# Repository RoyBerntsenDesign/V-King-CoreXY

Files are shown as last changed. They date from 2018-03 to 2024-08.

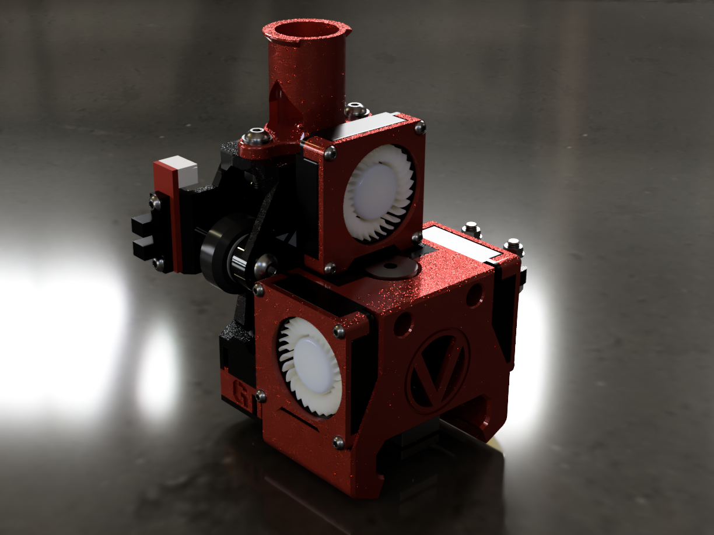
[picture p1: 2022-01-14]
Image Library/Renders/X-Carrier_Assy 4010 Fan Version 00.png

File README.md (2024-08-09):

# V-King Pro 3d Printer
The non rod CoreXY V-Slot 3d Printer by Roy Berntsen
In this repository you will find the print files and documentation for the V-King 3D printer

Here is a link to the Fusion 360 3d Model for viewing and also download: https://a360.co/3YxhjgS

You can be a supporter of the develompent on patreon here: https://www.patreon.com/pro3d?fan_landing=true
Or if you would buy me a coffe to keep the pace going in this project:

<a href="https://www.buymeacoffee.com/pro3d" target="_blank">Buy Me A Coffee</a>

Community links: https://www.facebook.com/vking3d/ - https://www.facebook.com/groups/viking3d/
Here is a video covering the basics and benefits of this design: https://youtu.be/wINF7qM0DQU

All files are released according to the following license unless specified differently in the file or directory:
CC-by-NC: http://creativecommons.org/licenses/by-nc/3.0/

Roy Berntsen - Research and Development

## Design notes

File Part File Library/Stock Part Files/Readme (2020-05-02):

Slicer Recomendations
Material: CPE, PETG or similar as is more durable than PLA

Walls:      2 mm Shell
Bottom/Top: 2 mm shell
Infill:		25% - 100%

You do need a good calibrated extruder as parts are tight so check your flow
All parts are modeled with tolerance to fit - Some holes are designed to be drilled

Suffix Explanation:
Example
- Filename_1x_SN_BN_100% = 1x of this part, Support NO, Brim NO, Infill 100%
- Filename_2x_SA_BY_25% = 2x of this part, Support ALL, Brim YES, Infill 25%
- Filename_3x_SB_BO_50% = 3x of this part, Support BUILDPLATE, Brim OPTIONAL, Infill 50%

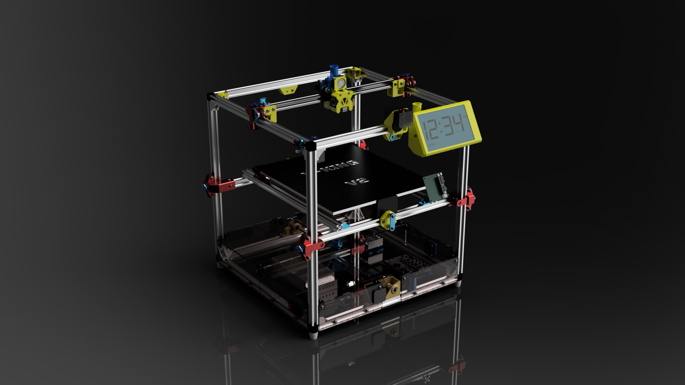
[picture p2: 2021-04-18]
V-King V2.0 00.PNG

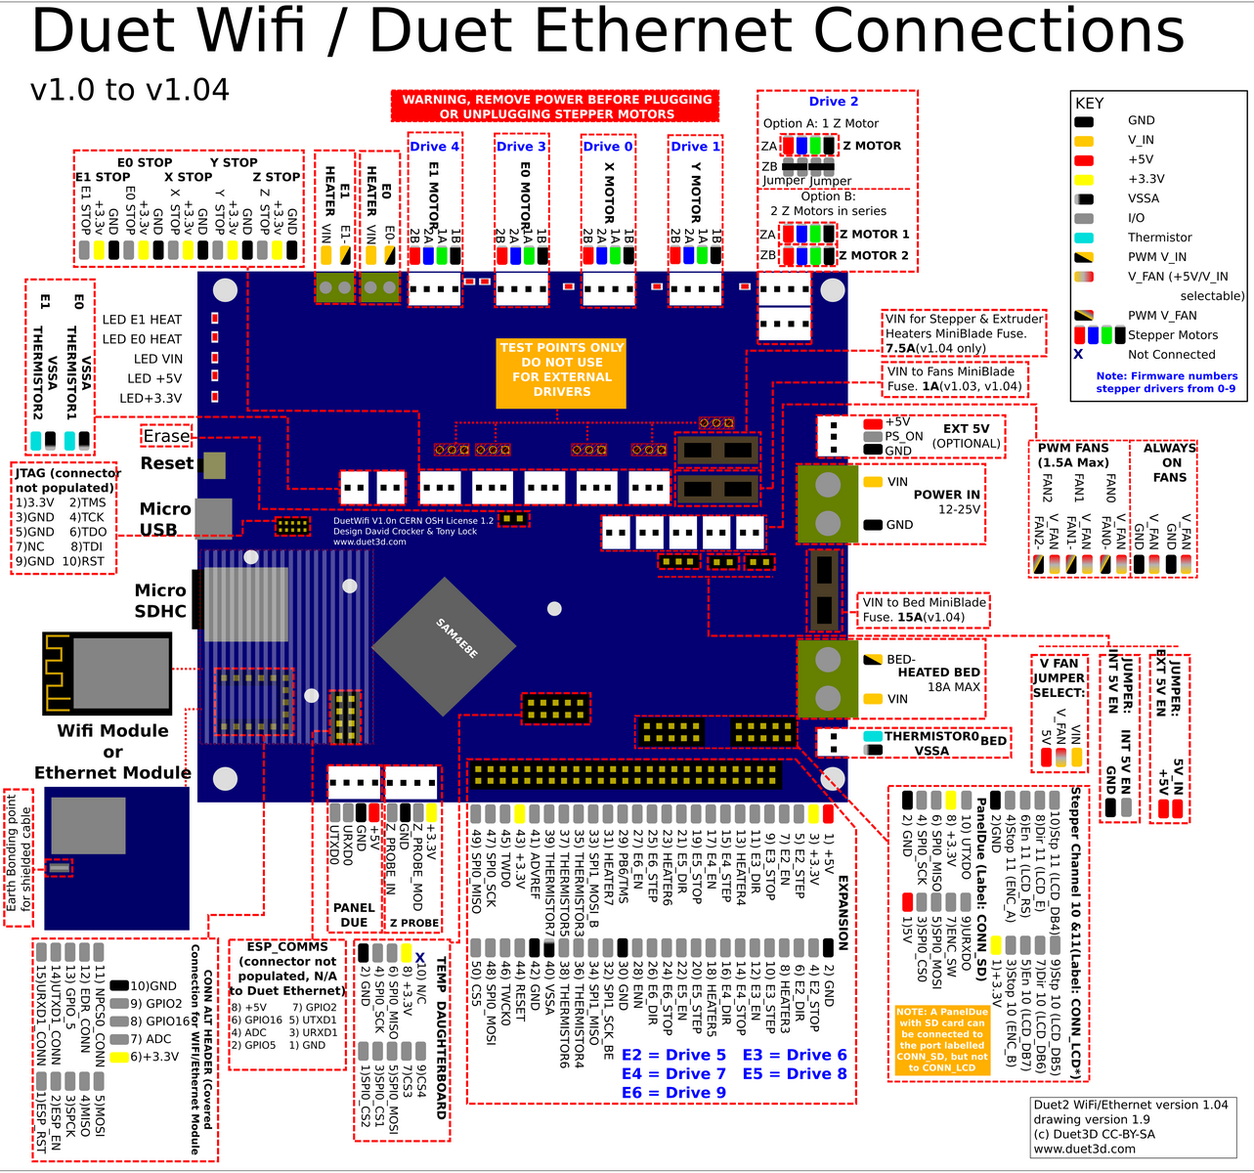
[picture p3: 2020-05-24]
Firmware Files/RRF-Duet/DuetWF Connection.png

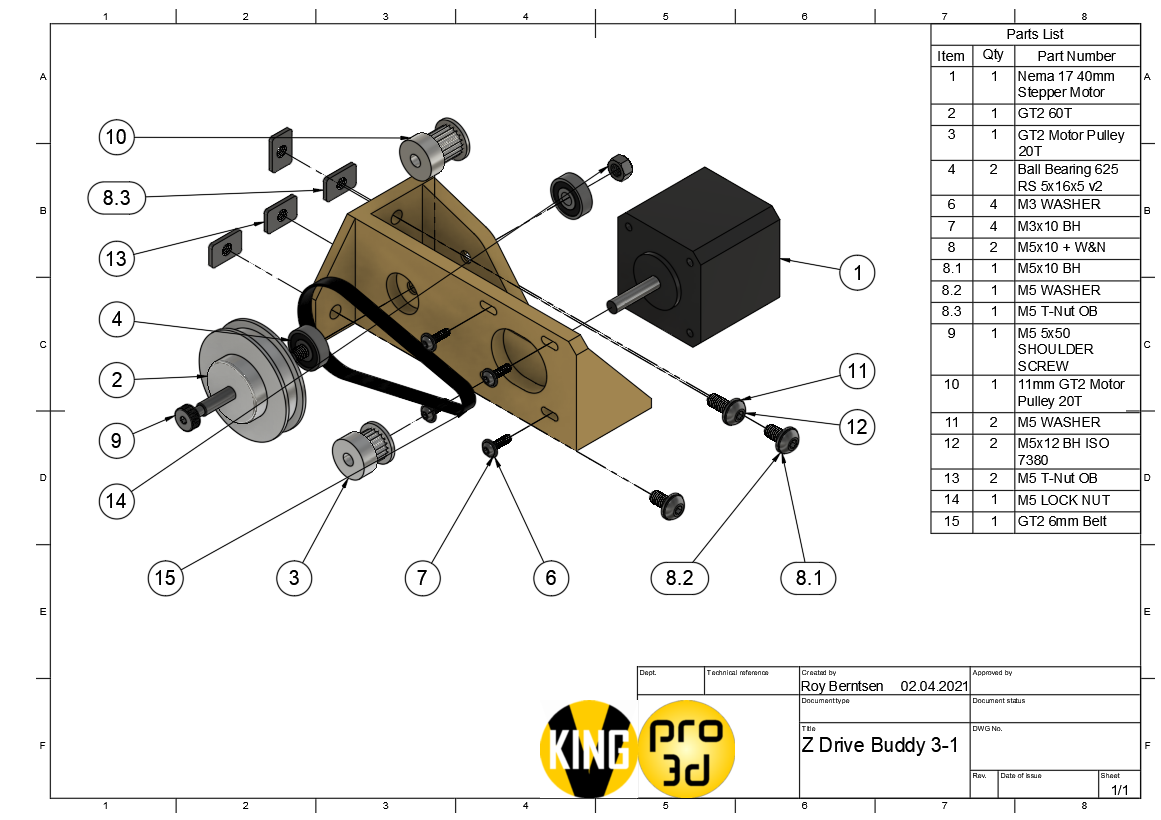
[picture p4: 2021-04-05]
Document Library/Drawings/GT2 Z BeltGear 00.png

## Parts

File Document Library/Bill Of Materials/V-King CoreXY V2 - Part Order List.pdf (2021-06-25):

V-King (https://www.buymeacoffee.com/pro3d) CoreXY Part List

MakerSupplies Mechanical Kit (https://makersupplies.dk/corexy-3d-printer/351-corexy-3d-printer-base-mechanical-kit-for-v-king-corexy-3d-printer.html) | <<-- ALL HARDWARE KIT HERE | | | $395,00
Component Part Name | Description | Quantity | Shop Link | Price | Optional Component | Price2
Belt GT2 Idler Smooth | GT2 20T Smooth Idler | 6 | 6Pcs 7mm Without T (http://s.click.aliexpress.com/e/b6kkkvj2) | $22,00
Belt GT2 Idler Thoothed | GT2 20T Thoothed Idler | 8 | 8Pcs 7mm With T (http://s.click.aliexpress.com/e/b6kkkvj2) | $25,00
Belt GT2 Stepper Motor Pulley | GT2 20T 6W 5mm Bore | 4 | 4 x 5 BORE (http://s.click.aliexpress.com/e/zhwLX5q) | $13,00
Belt GT2 Timing Belt 6mm | 10M 2GT Timing Belt 6W | 10 | 10M-6MM-2GT (http://s.click.aliexpress.com/e/cXFkq2jO) | $30,00
Belt Idler Precision Shim | 6,5mm OD/ 5mm ID Shim | 80 | (4x20) 6,5x5x1 Option Shim (https://www.aliexpress.com/item/32874078293.html?spm=2114.12010612.8148356.4.6b2842c5OC71Xu) | $20,00 | 200 pcs is same price (https://www.aliexpress.com/item/32874190317.html?spm=2114.12010612.8148356.2.6b2842c5nKhsGR)
Bowden Tube | 1.9ID 4OD Filament Tube | 1 | ID 1.9 OD 4 (http://s.click.aliexpress.com/e/cSMR0cdw) | $2,50
Cable Loom Tube | Sleeve for cables to hotend | 1 | 20mmx1m Cable Loom (https://s.click.aliexpress.com/e/_dTFkJul) | $2,50
Cable Nylon Sleeve | Sleeve for Heatbed cables | 1 | 5meter, 10mm Sleeve (https://s.click.aliexpress.com/e/_dVKCa4n) | $3,00
Controller Board | Duet WIFI Clone w/TMC2660 | 1 | MKS DUET WIFI Clone (https://s.click.aliexpress.com/e/_AsHC5n) | $60,00
Endstop Optical | XY(Z) Endstops | 3 | 6Pack Endstops (http://s.click.aliexpress.com/e/Im2VNR3) | $4,00
Extruder | BMG Clone Filament Extruder | 1 | TriangleLab BMG (https://s.click.aliexpress.com/e/_97d9QB) | $31,00
Fan for Controller Cooling | 4010 Axial Fan 12/24V | 1 | 24V Controller Fan (http://s.click.aliexpress.com/e/i1Q2ghS) | $3,00
Fan for Hotend Cooling | 4010 Blower Fan 12/24V | 1 | 24V 40x10 Blower (http://s.click.aliexpress.com/e/kHMx4q7O) | $2,00
Fan for Layer Cooling | 3010 Blower Fan 5/12 24V | 2 | 24V 30x30x10 (http://s.click.aliexpress.com/e/bele3ZZI) | $10,00
Heatbed Build Plate | Milled Cast Aluminum | 1 | 360x410x8 mm (https://makersupplies.dk/metal/816-metal-cnc-milled-cast-aluminum-plate.html) | $98,00
Heatbed Silicon Heater | 350*400 110V/220V Heater | 1 | 220V/110V (http://s.click.aliexpress.com/e/bWGHdGPI) | $16,00
Hotend | Dragon Hotend Clone | 1 | 1,75 24V Trianglelab Dragon (https://s.click.aliexpress.com/e/_ASb1l5) | $73,00
NEMA 17 1.8 A Stepper Motor | Stepper motor 1.5 Amp | 1x5 | 5Pack & Cable (https://s.click.aliexpress.com/e/_dXEZHHb) | $30,00
Power Switch | 10A 250VAC Fused Switch | 1 | 10A Fused Switch (http://s.click.aliexpress.com/e/blNcy7Lw) | $8,50
Powersupply | 24V 240W PSU | 1 | 24V 10A 240W (http://s.click.aliexpress.com/e/4GAsFeg) | $20,00
Safety Fuse | Thermal Safety Fuse for SSR | 1 | 135 Deg Fuse (http://s.click.aliexpress.com/e/bu7dz62U) | $2,00
Solid State Relay | Silicone Heater Relay Switch | 1 | SSR 40DA (http://s.click.aliexpress.com/e/ckUQTj4c) | $3,50
Worm Gear | 1:20 Worm Gear Set | 1 | Worm Gear (https://s.click.aliexpress.com/e/_A5bZW3) | $13,00 | High End Gear (https://makersupplies.dk/gear/361-gear-worm-gear-120-japan.html) | $51,00
Worm Gear Bearings | 5id-16od-5w Ball bearings | 10 | Worm Gear Bearings (http://s.click.aliexpress.com/e/c5afxP5q) | $4,00
Worm Gear Rod | 5mm X 555 mm Steel rod | 1 | Worm Gear Rod (https://rover.ebay.com/rover/1/711-53200-19255-0/1?icep_id=114&ipn=icep&toolid=20004&campid=5338443015) | $20,00
Z Leveling Probe | 3D Touch Leveling Probe | 1 | 3D Touch (http://s.click.aliexpress.com/e/bhxMAOUo) | $12,00
Component Total Price | | | | $528,00
Price inclusive mech kit | | | | USD 923,00

If you like to support - Buy me a coffe here:

https://www.buymeacoffee.com/pro3d

Research, Development & Design by:
Roy Berntsen M.Sc. Engineering Designer (https://www.buymeacoffee.com/pro3d)

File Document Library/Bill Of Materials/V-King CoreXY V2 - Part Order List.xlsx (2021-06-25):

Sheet: BOM Overview
V-King V2 Build Price Estimate
340x390x330 Build Volume
All aluminum, wheels and fastners | USD 395
Components Example Price: | USD 528
Cables and Connectors Estimated Price | USD 50
Tools - Add your number | USD 0
Sub Total Example Price | USD 973
Research - Development & Design by:
Roy Berntsen

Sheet: Complete Part List
 |  |  | V-King CoreXY Part List
MakerSupplies Mechanical Kit (https://makersupplies.dk/corexy-3d-printer/351-corexy-3d-printer-base-mechanical-kit-for-v-king-corexy-3d-printer.html) | <<-- ALL HARDWARE KIT HERE |  |  | $395.00
Component Part Name | Description | Quantity | Shop Link | Price | Optional Component | Price2
Belt GT2 Idler Smooth | GT2 20T Smooth Idler | 6 | 6Pcs 7mm Without T (http://s.click.aliexpress.com/e/b6kkkvj2) | $22.00
Belt GT2 Idler Thoothed | GT2 20T Thoothed Idler | 8 | 8Pcs 7mm With T (http://s.click.aliexpress.com/e/b6kkkvj2) | $25.00
Belt GT2 Stepper Motor Pulley | GT2 20T 6W 5mm Bore | 4 | 4 x 5 BORE (http://s.click.aliexpress.com/e/zhwLX5q) | $13.00
Belt GT2 Timing Belt 6mm | 10M 2GT Timing Belt 6W | 10 | 10M-6MM-2GT (http://s.click.aliexpress.com/e/cXFkq2jO) | $30.00
Belt Idler Precision Shim | 6,5mm OD/ 5mm ID Shim | 80 | (4x20) 6,5x5x1 Option Shim (https://www.aliexpress.com/item/32874078293.html?spm=2114.12010612.8148356.4.6b2842c5OC71Xu) | $20.00 | 200 pcs is same price (https://www.aliexpress.com/item/32874190317.html?spm=2114.12010612.8148356.2.6b2842c5nKhsGR)
Bowden Tube | 1.9ID 4OD Filament Tube | 1 | ID 1.9 OD 4 (http://s.click.aliexpress.com/e/cSMR0cdw) | $2.50
Cable Loom Tube | Sleeve for cables to hotend | 1 | 20mmx1m Cable Loom (https://s.click.aliexpress.com/e/_dTFkJul) | $2.50
Cable Nylon Sleeve | Sleeve for Heatbed cables | 1 | 5meter, 10mm Sleeve (https://s.click.aliexpress.com/e/_dVKCa4n) | $3.00
Controller Board | Duet WIFI Clone w/TMC2660 | 1 | MKS DUET WIFI Clone (https://s.click.aliexpress.com/e/_AsHC5n) | $60.00
Endstop Optical | XY(Z) Endstops | 3 | 6Pack Endstops (http://s.click.aliexpress.com/e/Im2VNR3) | $4.00
Extruder | BMG Clone Filament Extruder | 1 | TriangleLab BMG (https://s.click.aliexpress.com/e/_97d9QB) | $31.00
Fan for Controller Cooling | 4010 Axial Fan 12/24V | 1 | 24V Controller Fan (http://s.click.aliexpress.com/e/i1Q2ghS) | $3.00
Fan for Hotend Cooling | 4010 Blower Fan 12/24V | 1 | 24V 40x10 Blower (http://s.click.aliexpress.com/e/kHMx4q7O) | $2.00
Fan for Layer Cooling | 3010 Blower Fan 5/12 24V | 2 | 24V 30x30x10 (http://s.click.aliexpress.com/e/bele3ZZI) | $10.00
Heatbed Build Plate | Milled Cast Aluminum | 1 | 360x410x8 mm (https://makersupplies.dk/metal/816-metal-cnc-milled-cast-aluminum-plate.html) | $98.00
Heatbed Silicon Heater | 350*400 110V/220V Heater | 1 | 220V/110V (http://s.click.aliexpress.com/e/bWGHdGPI) | $16.00
Hotend | Dragon Hotend Clone | 1 | 1,75 24V Trianglelab Dragon (https://s.click.aliexpress.com/e/_ASb1l5) | $73.00
NEMA 17 1.8 A Stepper Motor | Stepper motor 1.5 Amp | 1x5 | 5Pack & Cable (https://s.click.aliexpress.com/e/_dXEZHHb) | $30.00
Power Switch | 10A 250VAC Fused Switch | 1 | 10A Fused Switch (http://s.click.aliexpress.com/e/blNcy7Lw) | $8.50
Powersupply | 24V 240W PSU | 1 | 24V 10A 240W (http://s.click.aliexpress.com/e/4GAsFeg) | $20.00
Safety Fuse | Thermal Safety Fuse for SSR | 1 | 135 Deg Fuse (http://s.click.aliexpress.com/e/bu7dz62U) | $2.00
Solid State Relay | Silicone Heater Relay Switch | 1 | SSR 40DA (http://s.click.aliexpress.com/e/ckUQTj4c) | $3.50
Worm Gear | 1:20 Worm Gear Set | 1 | Worm Gear (https://s.click.aliexpress.com/e/_A5bZW3) | $13.00 | High End Gear (https://makersupplies.dk/gear/361-gear-worm-gear-120-japan.html) | $51.00
Worm Gear Bearings | 5id-16od-5w Ball bearings | 10 | Worm Gear Bearings (http://s.click.aliexpress.com/e/c5afxP5q) | $4.00
Worm Gear Rod | 5mm X 555 mm Steel rod | 1 | Worm Gear Rod (https://rover.ebay.com/rover/1/711-53200-19255-0/1?icep_id=114&ipn=icep&toolid=20004&campid=5338443015) | $20.00
Z Leveling Probe | 3D Touch Leveling Probe | 1 | 3D Touch (http://s.click.aliexpress.com/e/bhxMAOUo) | $12.00
Component Total Price |  |  |  | $528.00
Price inclusive mech kit |  |  |  | USD 923.00

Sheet: Fasteners BOM
Part name | Quantity | Order Quantity | Est. Price
M2,0x06 BH | 2 |  | 0.15 | 0.3
M2,5x12 BH | 2 |  | 0.15 | 0.3
M2,5x16 BH | 2 |  | 0.15 | 0.3
M3 Lock Nut | 2 |  | 0.15 | 0.3
M3 NUT | 14 |  | 0.15 | 2.1
M3 WASHER | 14 |  | 0.15 | 2.1
M3x08 BH | 10 |  | 0.15 | 1.5
M3x12 BH | 4 |  | 0.15 | 0.6
M3x20 BH | 6 |  | 0.15 | 0.9
M3x25 BH | 4 |  | 0.15 | 0.6
M4 NUT | 4 |  | 0.15 | 0.6
M4 WASHER | 4 |  | 0.15 | 0.6
M4x12 BH | 2 |  | 0.15 | 0.3
M4x16 BH | 4 |  | 0.15 | 0.6
M5 Hammer-Nut | 16 | 25 | 0.15 | 2.4
M5 Lock Nut | 23 | 25 | 0.15 | 3.45
M5 Nut | 19 | 25 | 0.15 | 2.85
M5 T-Nut OB | 110 |  | 0.15 | 16.5
M5 WASHER | 166 | 175 | 0.15 | 24.9
M5x08 Countersink | 24 |  | 0.15 | 3.6
M5x10 BH | 142 | 150 | 0.15 | 21.3
M5x20 Hex | 9 |  | 0.15 | 1.35
M5x25 BH | 13 |  | 0.15 | 1.95
M5x30 Button Head | 12 |  | 0.15 | 1.8
M5x35 BH | 2 |  | 0.15 | 0.3
M5x35 Hex | 4 |  | 0.15 | 0.6
M5x40 BH | 2 |  | 0.15 | 0.3
M5x6,5x1 Precision Shim | 73 | 80 | 0.15 | 10.95
Est sub total fastners: |  |  |  | $103.35

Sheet: Tools
Tools
Crimping Tool | PA-21 (http://rover.ebay.com/rover/1/711-53200-19255-0/1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) | 40

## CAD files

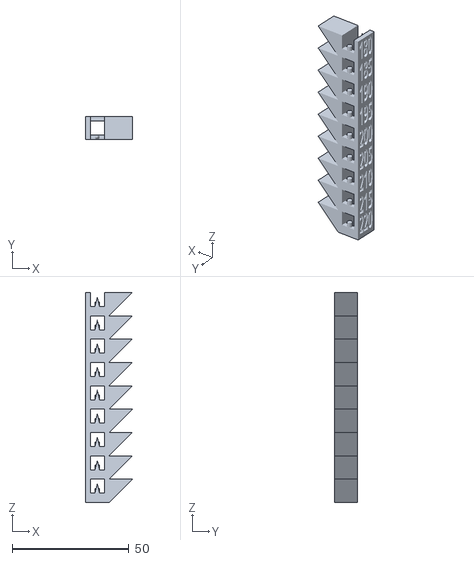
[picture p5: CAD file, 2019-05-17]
Calibration Files/Temp Tower.stl
20.0 x 10.0 x 90.0

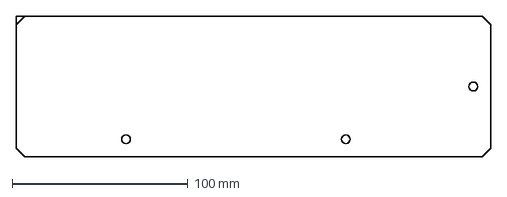
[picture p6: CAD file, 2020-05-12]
Document Library/Drawings/Cabinet Cut Pattern/Panel Side A_2x.dxf
270.0 x 80.0 mm

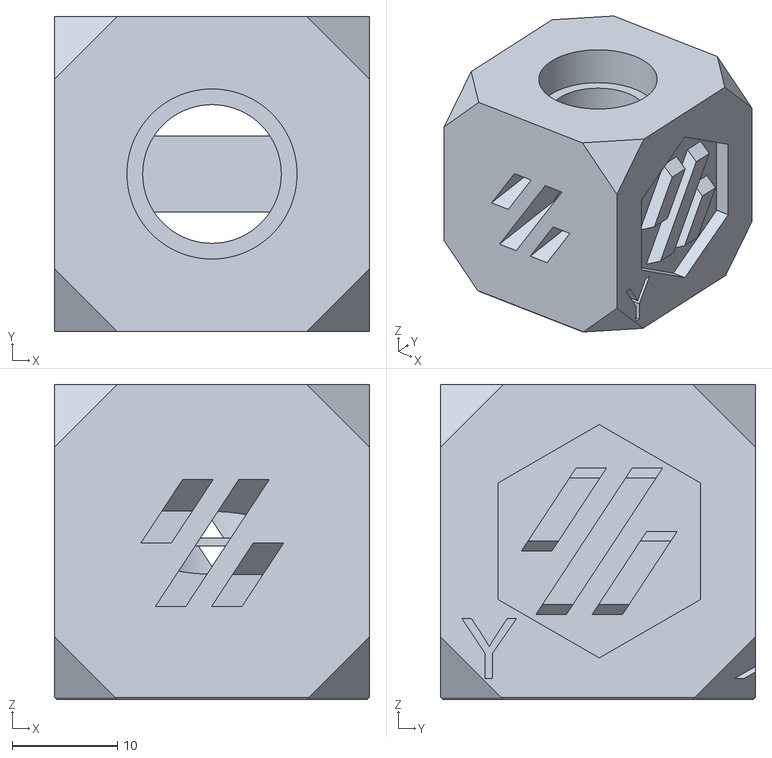
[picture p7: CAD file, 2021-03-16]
Part File Library/Calibration Files/Voron_Design_Cube_v7 (1).stl
30.0 x 30.0 x 30.0

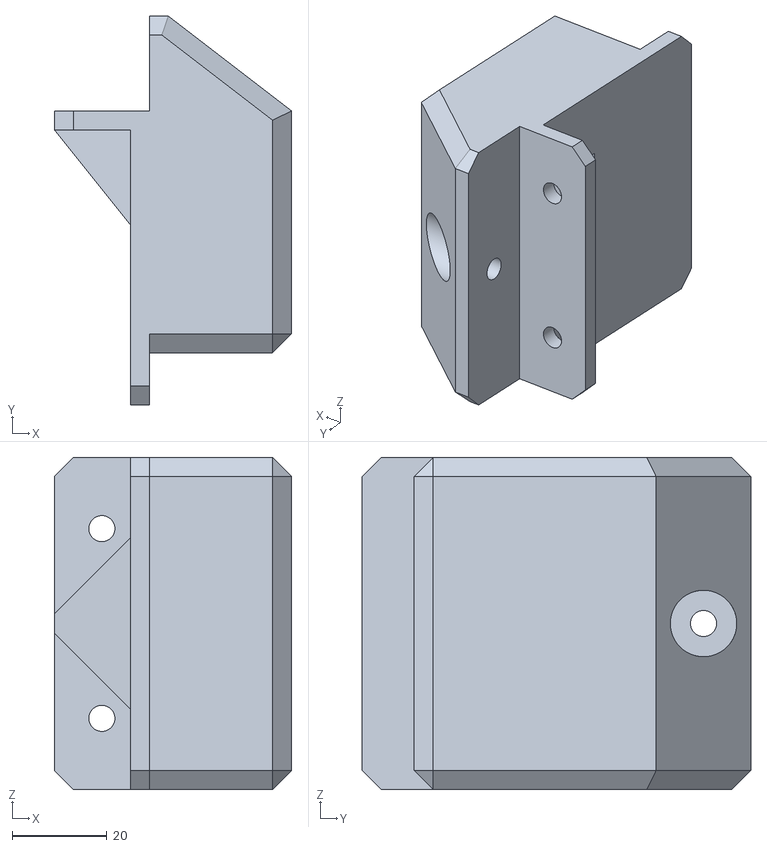
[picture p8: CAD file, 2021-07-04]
Part File Library/Discontinued Files/3P Center Bed Support V1.1_1x_SN_BN.stl
50.0 x 82.0 x 70.0

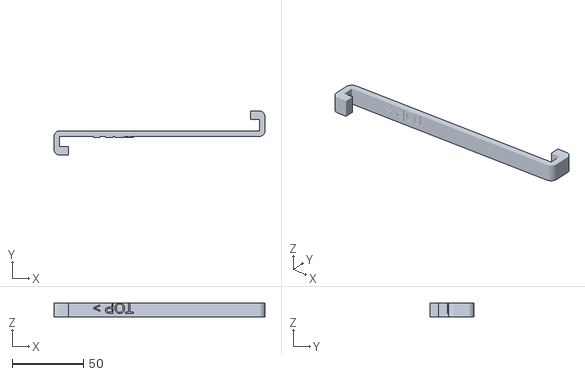
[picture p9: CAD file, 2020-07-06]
Part File Library/Optional Files/Bed Frame Hooks_4x_SN_BO.stl
148.0 x 31.0 x 10.0

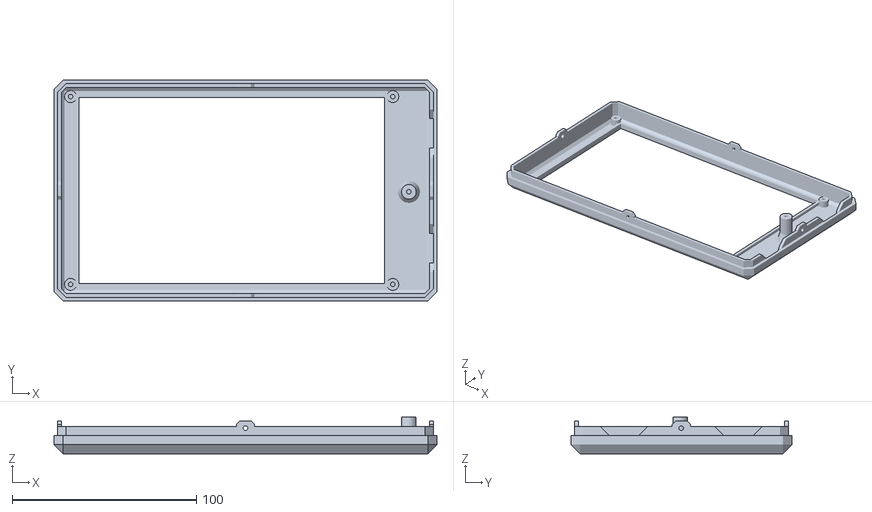
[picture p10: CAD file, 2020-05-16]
Part File Library/Optional Files/Panel Due 7in Cabinet Combo/Panel Due Cabinet Panel_1x_SN_BN.stl
208.0 x 120.0 x 20.0

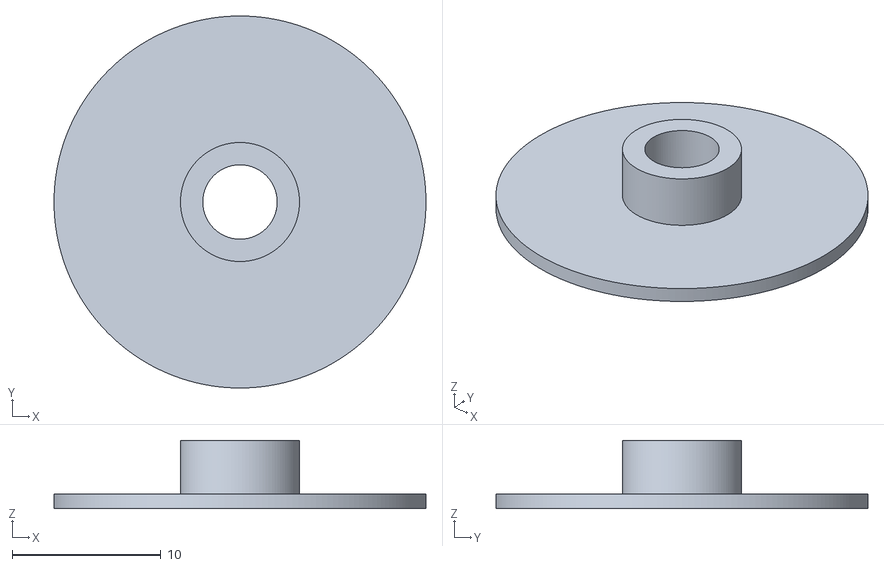
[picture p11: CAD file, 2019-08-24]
Part File Library/Optional Files/XY Belt Tensioner/608 Bearing Adapter_4x_SN_BN.stl
25.0 x 25.0 x 4.60

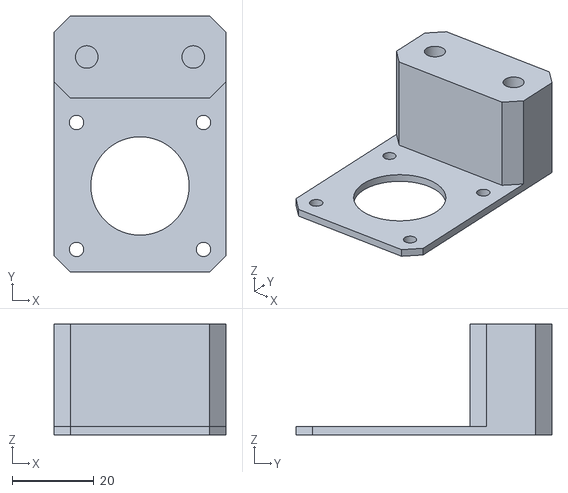
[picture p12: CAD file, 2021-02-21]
Part File Library/Stock Part Files/Base Frame Parts/Extruder Buddy_1x_SN_BN.stl
42.0 x 62.5 x 27.0

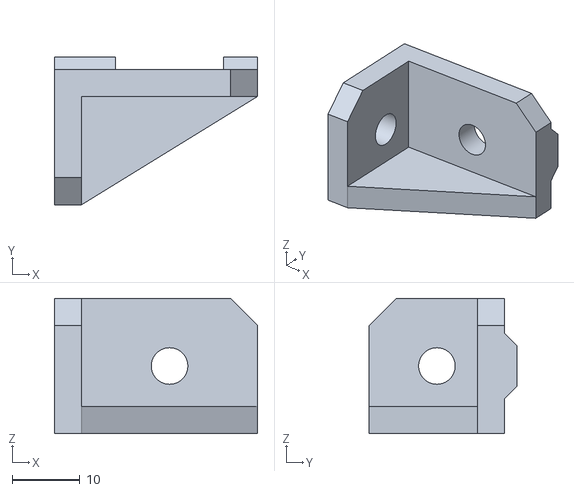
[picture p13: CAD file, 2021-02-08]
Part File Library/Stock Part Files/Bed Frame Parts/Bed L Bracket_4x_SN_BN.stl
30.0 x 21.8 x 20.0

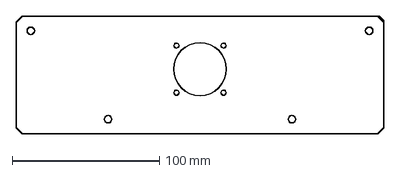
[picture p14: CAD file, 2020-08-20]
Part File Library/Stock Part Files/Bottom Cabinet Files/Cabinet Cut Pattern/Panel Side Fan_1x.dxf
250.0 x 80.0 mm

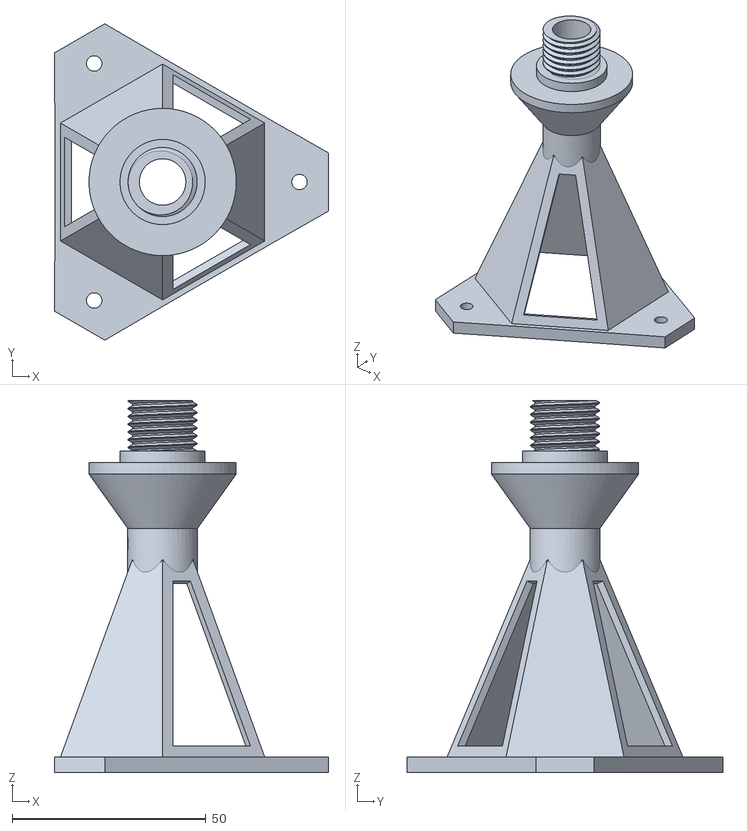
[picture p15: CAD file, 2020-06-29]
Part File Library/Stock Part Files/Bottom Cabinet Files/Cabinet Lid Support_1x_SN_BO.stl
70.7 x 81.7 x 96.0

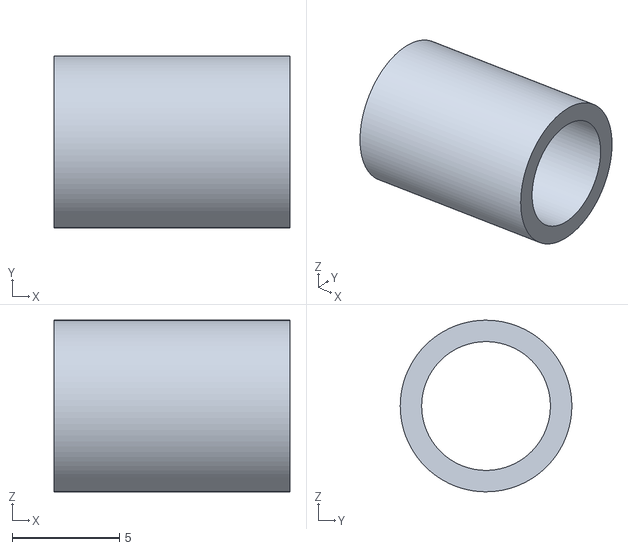
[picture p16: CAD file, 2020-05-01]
Part File Library/Stock Part Files/X Axis Parts/X Axis Idler Spacer_2x_SN_BY.stl
11.0 x 8.00 x 8.00

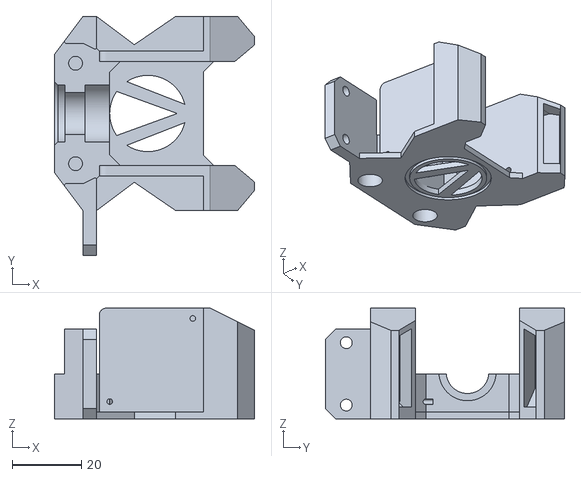
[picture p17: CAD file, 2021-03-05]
Part File Library/Stock Part Files/X Axis Parts/X Carrier/X Carrier Hotend Buddy_1x_SA_BN.stl
57.9 x 69.0 x 32.0

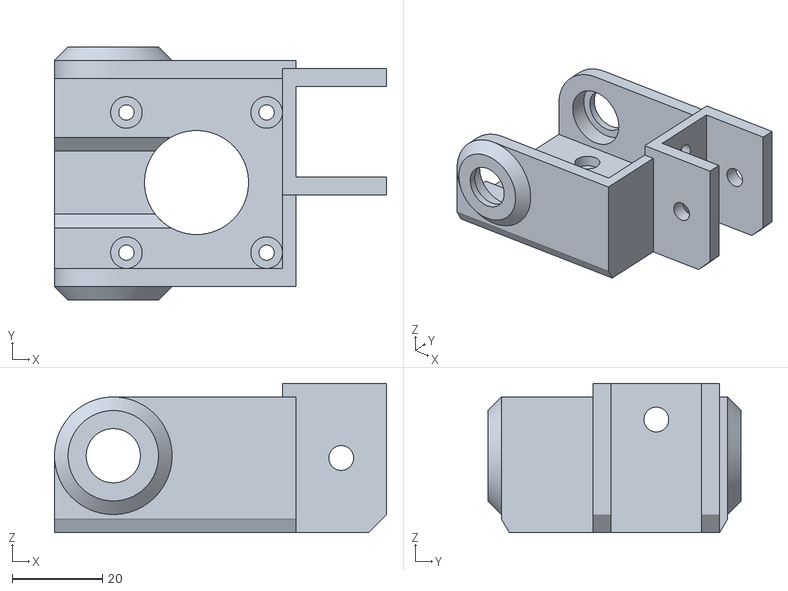
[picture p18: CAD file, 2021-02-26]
Part File Library/Stock Part Files/Z Drive Parts/Z Worm Gear Buddy_1x_SN_BN.stl
73.4 x 56.0 x 33.0

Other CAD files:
Part Print Files/Upgrade STL Files/Tablet Buddy.stl
Part Print Files/Z Part Files/Bed Belt Idler Support.stl
Source File Library/X Carrier Hotend Buddy.step
Source Files/Slider Fork v1.step
Calibration Files/3020 Cylinder.stl
Calibration Files/303010 Calibration Cube.stl
Calibration Files/Stringing_Test.stl
Calibration Files/xyzCalibration_cube.stl
Part File Library/Calibration Files/3020 Cylinder.stl
Part File Library/Calibration Files/303010 Calibration Cube.stl
Part File Library/Calibration Files/Retract four_square_cons.stl
Part File Library/Calibration Files/Stringing_Test.stl
Part File Library/Calibration Files/xyzCalibration_cube.stl
Part File Library/Calibration Files/z-wobble-test-square.stl
Part File Library/Calibration Files/z-wobble-test.stl
Part File Library/Optional Files/Panel Due 7in Cabinet Combo/Panel Due Cabinet Base_1x_SB_BN.stl
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

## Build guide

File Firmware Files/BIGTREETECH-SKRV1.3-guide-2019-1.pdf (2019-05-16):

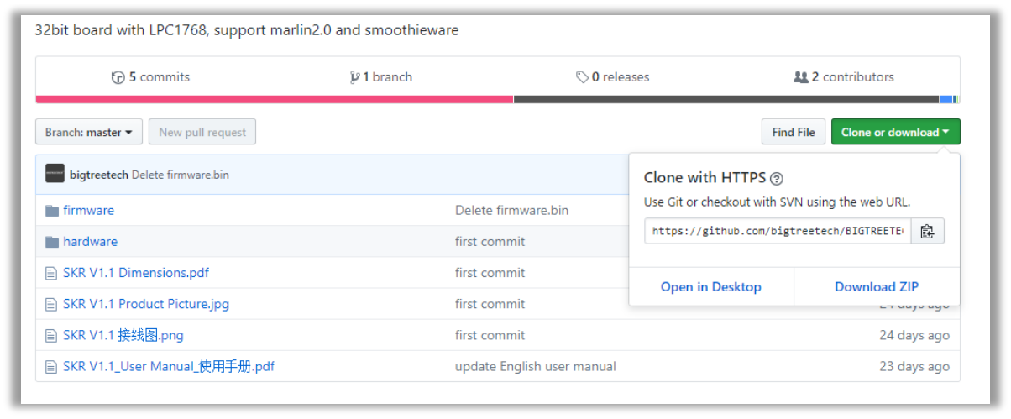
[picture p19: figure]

BIGTREETECH SKR V1.3 guide 2019 – V1 by Jupa Creations Page 1

BIGTREETECH/BIQU SKR V1.3 instruction guide by Jupa Creations

All official information like schematics and hardware about this 32 bits 3D printer mainboard can be found on the BIGTREETECH official GITHUB site. (https://github.com/bigtreetech/BIGTREETECH-SKR-V1.3)

This instruction guide is to show you how to install Marlin 2.0 firmware to the SKR V1.3 board in general. It does not take in account machine and other hardware specific settings!

You can use VSCode or Atom.IO + Platform IO to compile Marlin2.0 to BIGTREETECH/BIQU SKR V1.3

Intended for use with a REPRAP_DISCOUNT_FULL_GRAPHIC_SMART_CONTROLLER 128x64 LCD display by standard with two 10 wire ribbon cables.

Download the Marlin2.0 firmware from Marlin 2.0 github firmware version (https://github.com/MarlinFirmware/Marlin/tree/bugfix-2.0.x) and click.

Click “Download ZIP”

Remark if you use Octoprint, do not use the BIGTREETECH firmware version itself but download Marlin 2.0 github firmware version (https://github.com/MarlinFirmware/Marlin/tree/bugfix-2.0.x) and modify it to your needs.

When the download is complete, unzip the file to a known place.

N this example we use VScode

Download the VScode from https://code.visualstudio.com/Download. Choose the version which is compliant with your PC operating system.

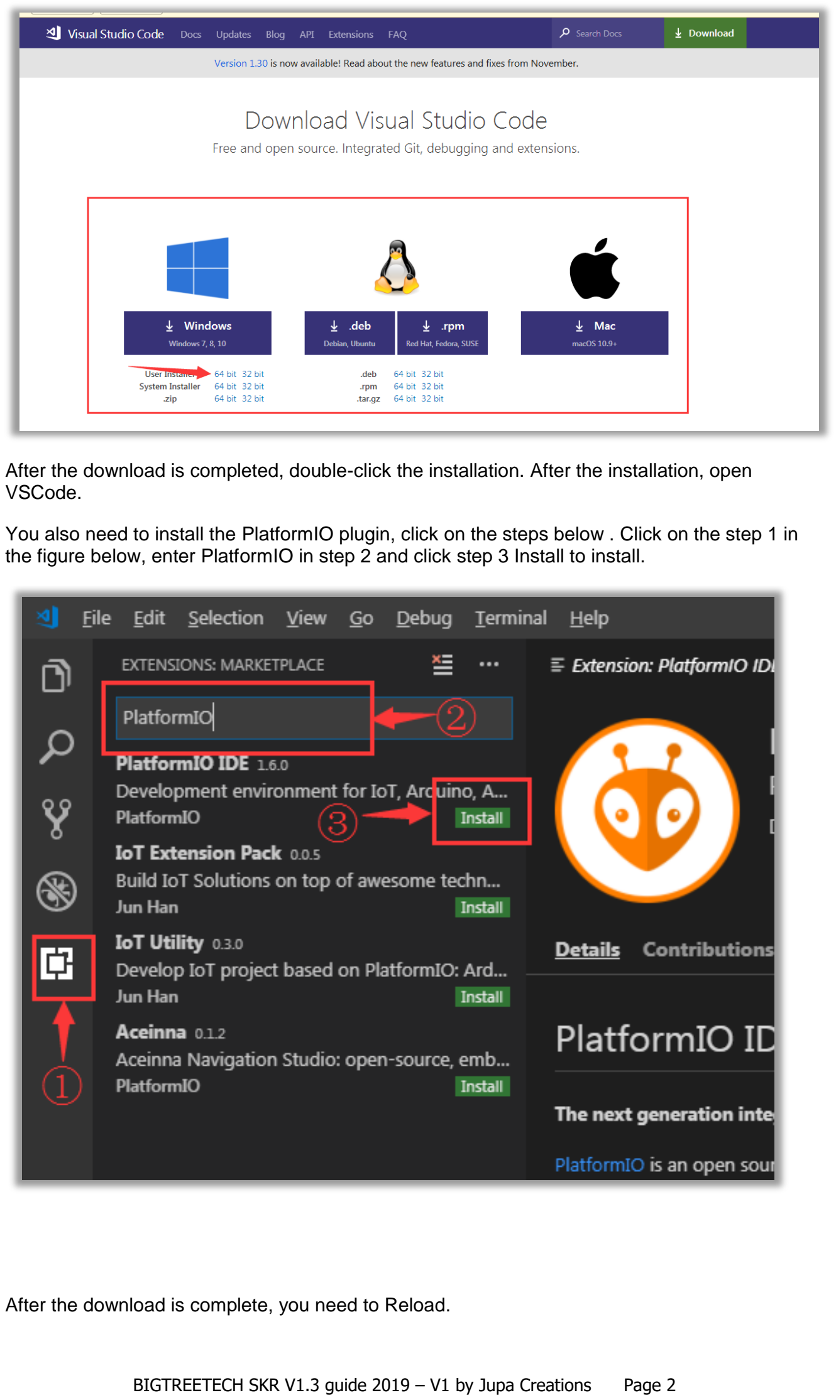
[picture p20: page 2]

BIGTREETECH SKR V1.3 guide 2019 – V1 by Jupa Creations Page 2

After the download is completed, double-click the installation. After the installation, open VSCode.

You also need to install the PlatformIO plugin, click on the steps below . Click on the step 1 in the figure below, enter PlatformIO in step 2 and click step 3 Install to install.

After the download is complete, you need to Reload.

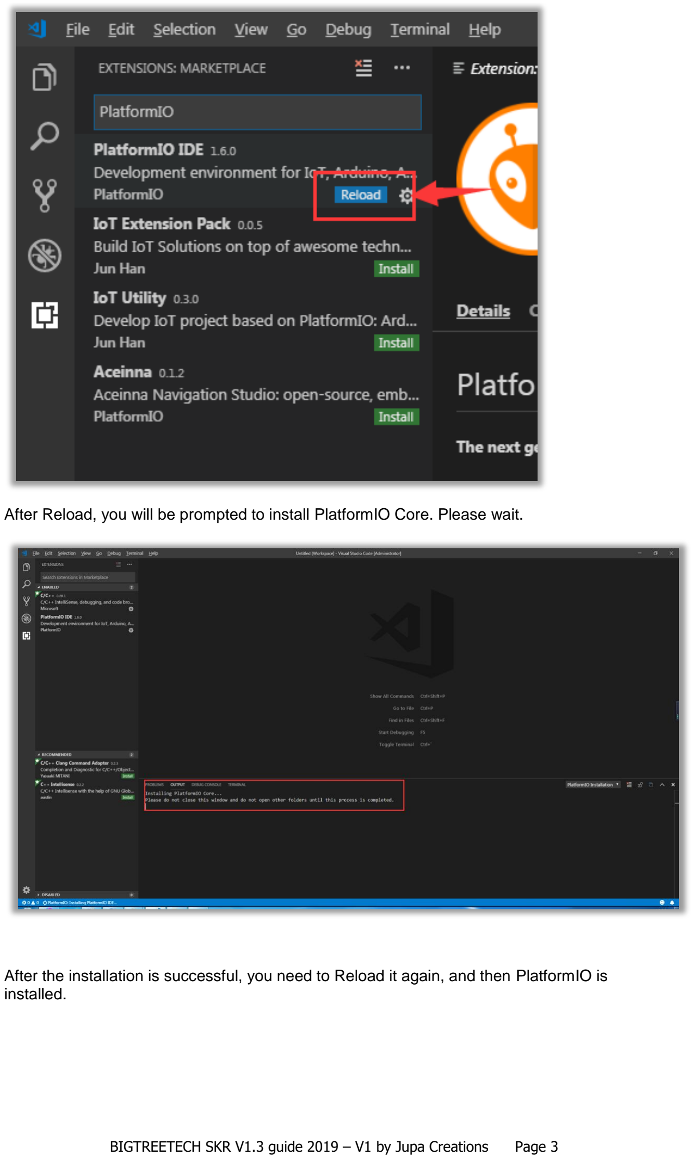
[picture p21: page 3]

BIGTREETECH SKR V1.3 guide 2019 – V1 by Jupa Creations Page 3

After Reload, you will be prompted to install PlatformIO Core. Please wait.

After the installation is successful, you need to Reload it again, and then PlatformIO is installed.

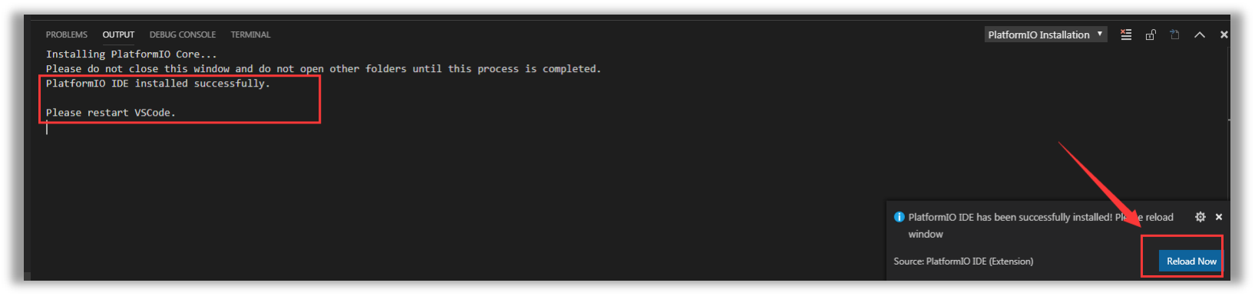
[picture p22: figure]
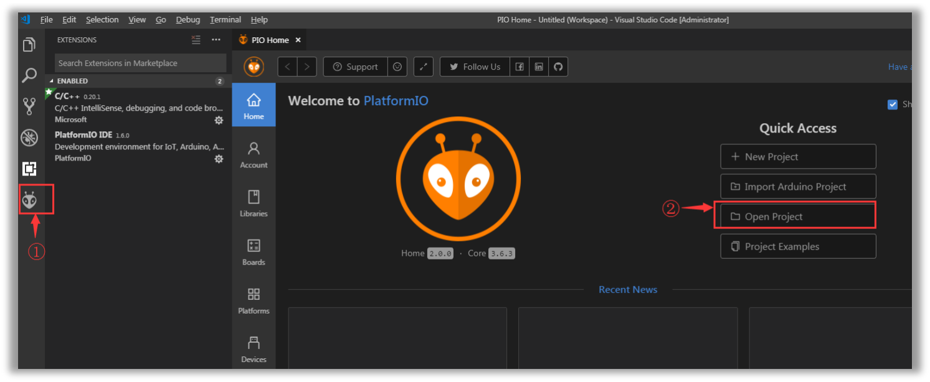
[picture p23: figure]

BIGTREETECH SKR V1.3 guide 2019 – V1 by Jupa Creations Page 4

In the lower left corner of VSCode, you can see the icon (1), which is PlatformIO plug-in. Click
(2) Open Project to Open the Project.

Find the marlin2.0 source directory where you extracted in the very first step, and click Open.

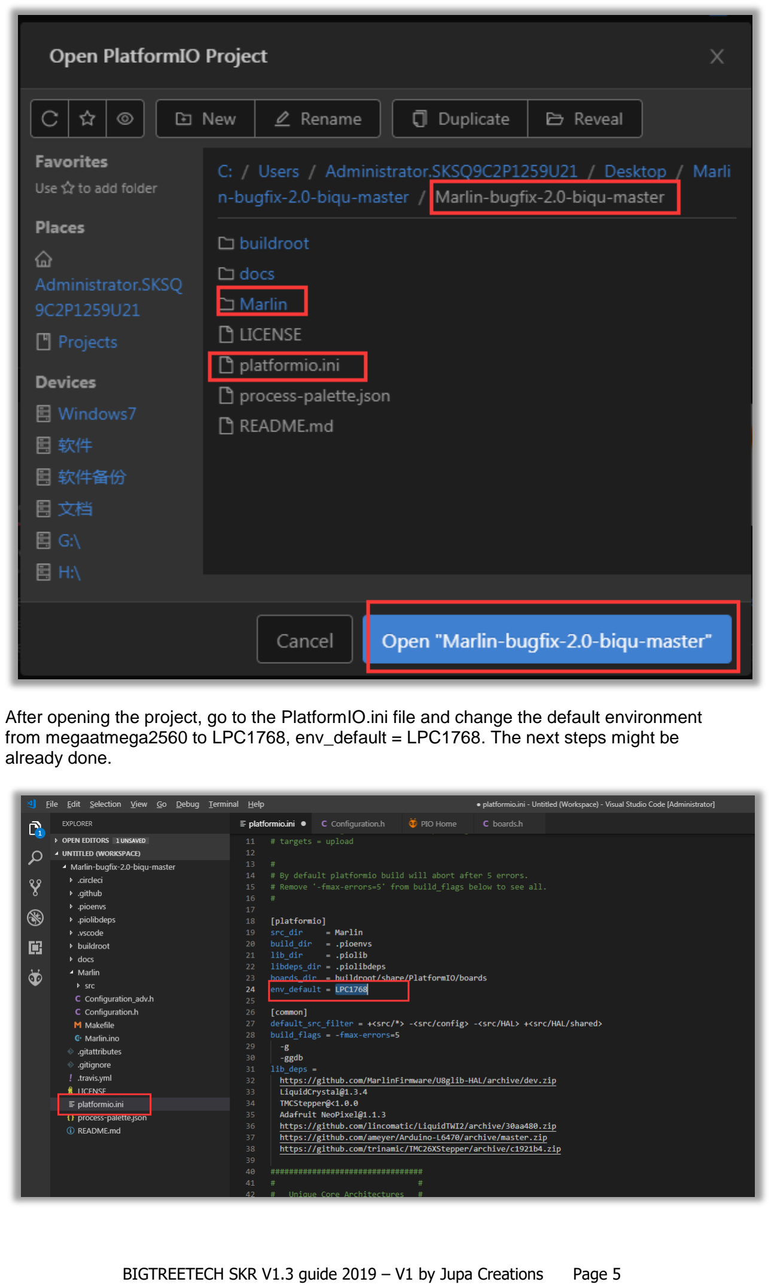
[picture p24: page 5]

BIGTREETECH SKR V1.3 guide 2019 – V1 by Jupa Creations Page 5

After opening the project, go to the PlatformIO.ini file and change the default environment from megaatmega2560 to LPC1768, env_default = LPC1768. The next steps might be already done.

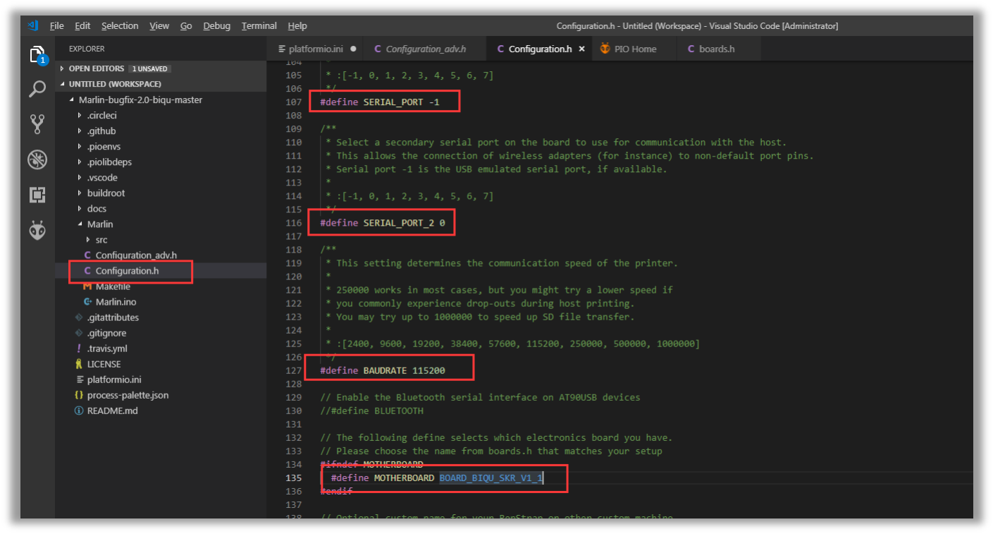
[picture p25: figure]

BIGTREETECH SKR V1.3 guide 2019 – V1 by Jupa Creations Page 6

Then go to the configuration.h file and if not yet done modify it to

#define SERIAL_PORT 0

#define SERIAL_PORT_2 -1

#define BAUDRATE 115200

#define MOTHERBOARD BOARD_BIQU_SKR_V1_3

If you like to use a BL-touch you have to change some code.

In the same Configuration.h

Modify the following lines:

//#define BLTOUCH and change to
#define BLTOUCH

//#define AUTO_BED_LEVELING_BILINEAR and change to #define AUTO_BED_LEVELING_BILINEAR

// #define Z_SAFE_HOMING and change to
#define Z_SAFE_HOMING

// #define ENCODER_PULSES_PER_STEP 4 and change to #define ENCODER_PULSES_PER_STEP 4

// #define REVERSE_ENCODER_DIRECTION and change to
#define REVERSE_ENCODER_DIRECTION

//#define REPRAP_DISCOUNT_FULL_GRAPHIC_SMART_CONTROLLER and change to #define REPRAP_DISCOUNT_FULL_GRAPHIC_SMART_CONTROLLER

If you like to activate Babystepping switch to Configuration_adv.h

//#define BABYSTEPPING and change to
#define BABYSTEPPING

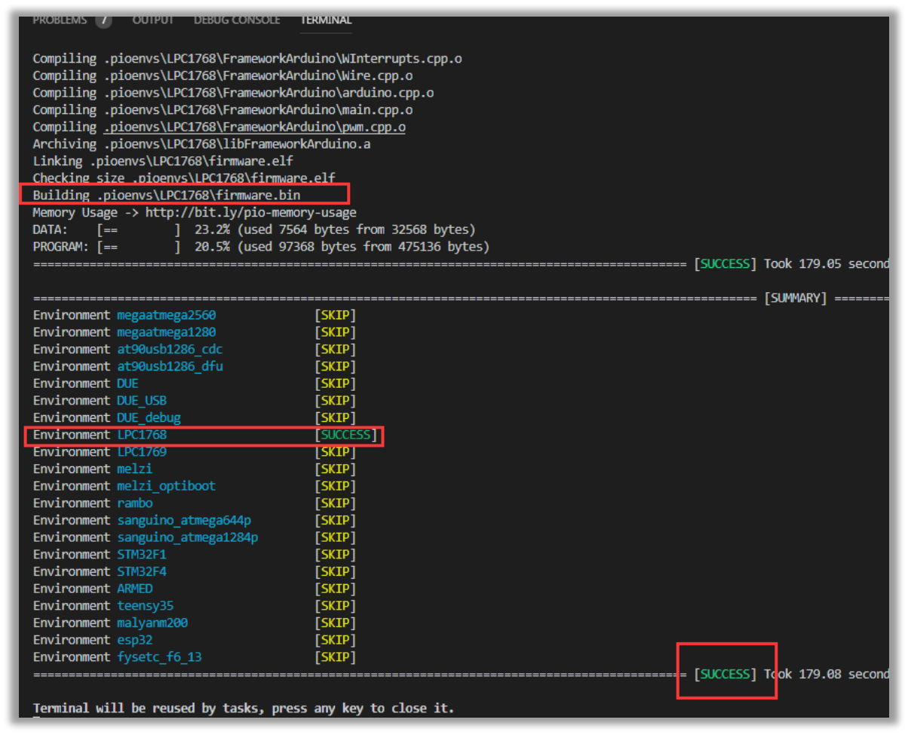
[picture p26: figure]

BIGTREETECH SKR V1.3 guide 2019 – V1 by Jupa Creations Page 7

//#define DOUBLECLICK_FOR_Z_BABYSTEPPING and change to #define DOUBLECLICK_FOR_Z_BABYSTEPPING

//#define BABYSTEP_ZPROBE_OFFSET and change to #define BABYSTEP_ZPROBE_OFFSET

//#define BABYSTEP_ZPROBE_GFX_OVERLAY and change to #define BABYSTEP_ZPROBE_GFX_OVERLAY

#define BABYSTEP_MULTIPLICATOR 1 and change to

#define BABYSTEP_MULTIPLICATOR 20

If your original BL-touch, clone TL-touch or clone BT-touch is dropping the pin during printing switch to Marlin/scr/inc/conditionals_LCD.h and change the following code:

#define BLTOUCH_STOW 100 // was 90

#define BLTOUCH_SELFTEST 130 // was 120

After the modification is completed, for VScode press the Ctrl+Shift+B keys to start compiling. PlatformIO will automatically download the compile component and then compile.

Compiling can take up to 5 minutes, so be patient.

After the compiling is successful, a “firmware.bin” file will be generated in the \pioenvs\LPC1768 directory. Copy this file to the TF card of the motherboard and reset or powercycle the motherboard, so that the firmware is burned into the motherboard.

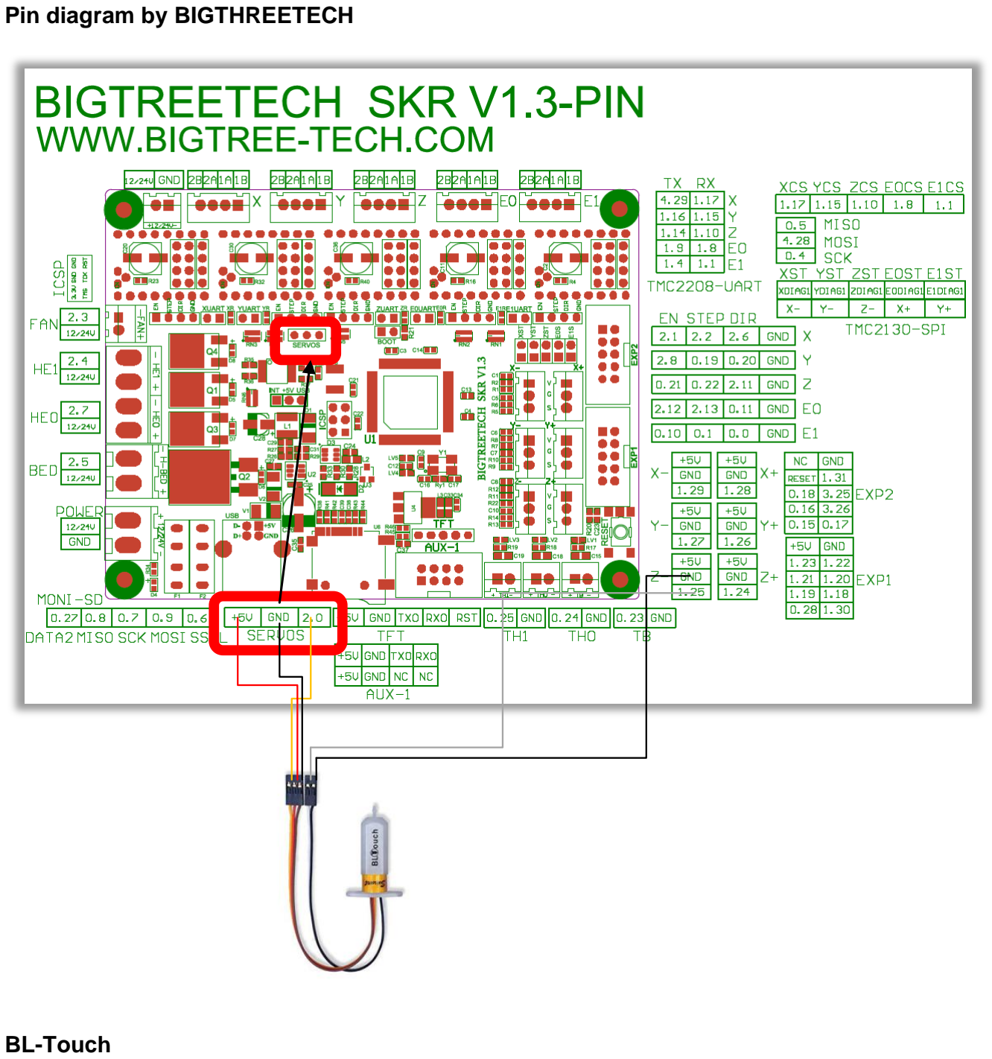
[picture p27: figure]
Pin diagram by BIGTHREETECH; BL-Touch

BIGTREETECH SKR V1.3 guide 2019 – V1 by Jupa Creations Page 8

The SKR V1.3 board has a dedicated Servo port.

Wire connections need to be checked before use!

For connecting the ANTCLABS BL-touch three wire cable to Servo port.
SKR V1.3 Board servo port = (+)(-)(puls) and BL-touch = (-)(+)(puls)
Positive (+) and Minus (-) need to be swapped in the BL-Touch connector or an intermediate connection cable need to be made. The two wire sensor cable connects to the (Z-) port.

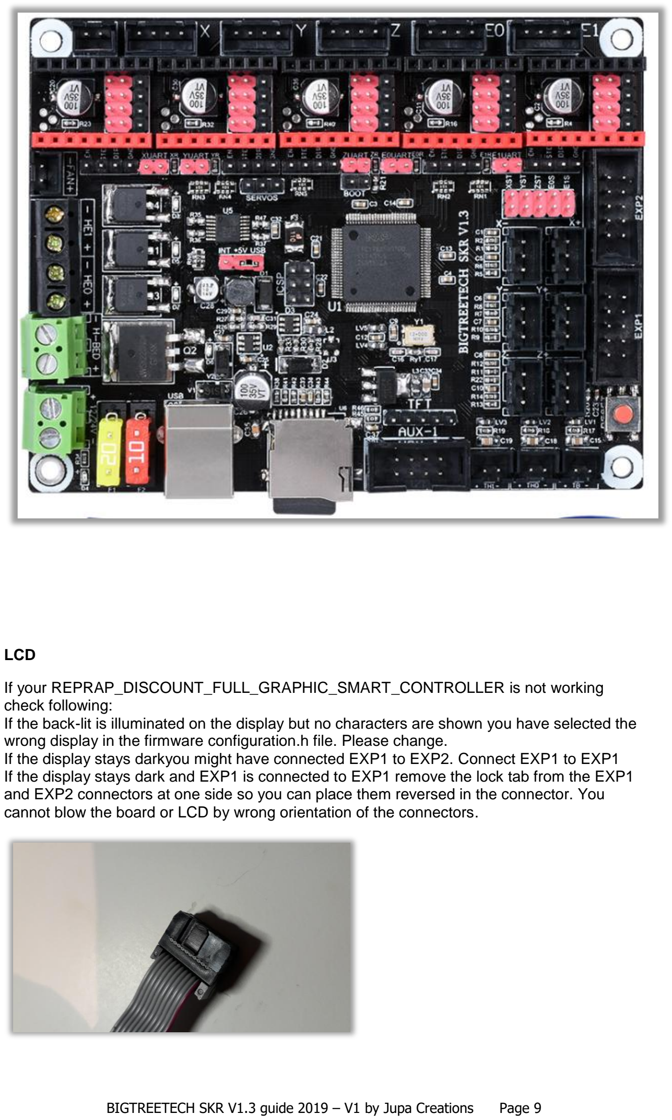
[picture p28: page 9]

BIGTREETECH SKR V1.3 guide 2019 – V1 by Jupa Creations Page 9

LCD

If your REPRAP_DISCOUNT_FULL_GRAPHIC_SMART_CONTROLLER is not working check following:
If the back-lit is illuminated on the display but no characters are shown you have selected the wrong display in the firmware configuration.h file. Please change.
If the display stays darkyou might have connected EXP1 to EXP2. Connect EXP1 to EXP1 If the display stays dark and EXP1 is connected to EXP1 remove the lock tab from the EXP1 and EXP2 connectors at one side so you can place them reversed in the connector. You cannot blow the board or LCD by wrong orientation of the connectors.

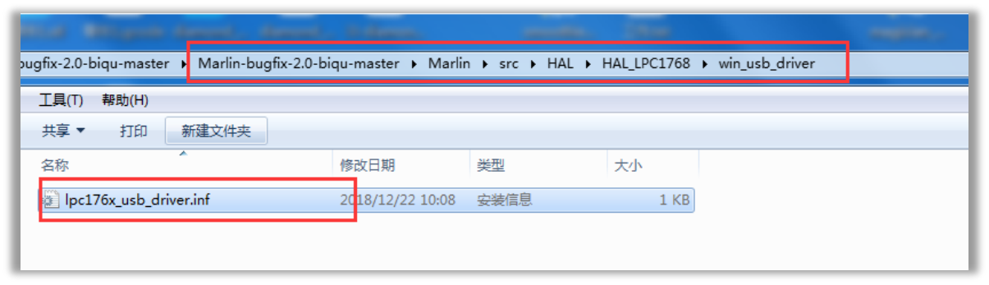
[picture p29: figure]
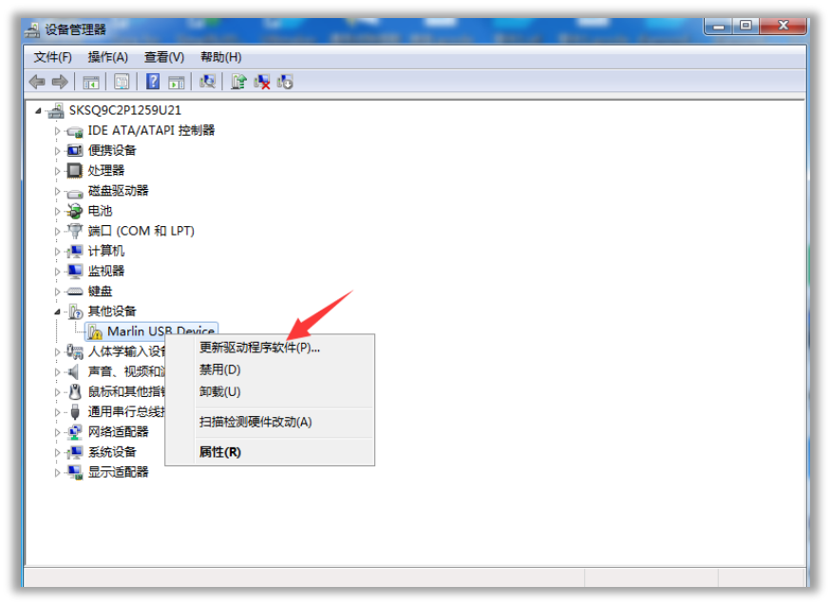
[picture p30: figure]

BIGTREETECH SKR V1.3 guide 2019 – V1 by Jupa Creations Page 10

In Windows 10 a driver called MARLIN will be automatically installed by plug & play when a USB cable is connected to the motherboard. It will show as a MARLIN port. Do not install any other USB driver or Smoothie drivers while usng Windows 10!

For other Windows operating systems the computer identification motherboard needs to install USB to serial port driver manually in the directory of the firmware as shown below. Because its path is too long, copy it to an easy to find location like to the desktop.

Open the Device manager, you can see that there is an unrecognized Marlin USB Device, click to update the driver software.

Browse the computer to find the driver software.

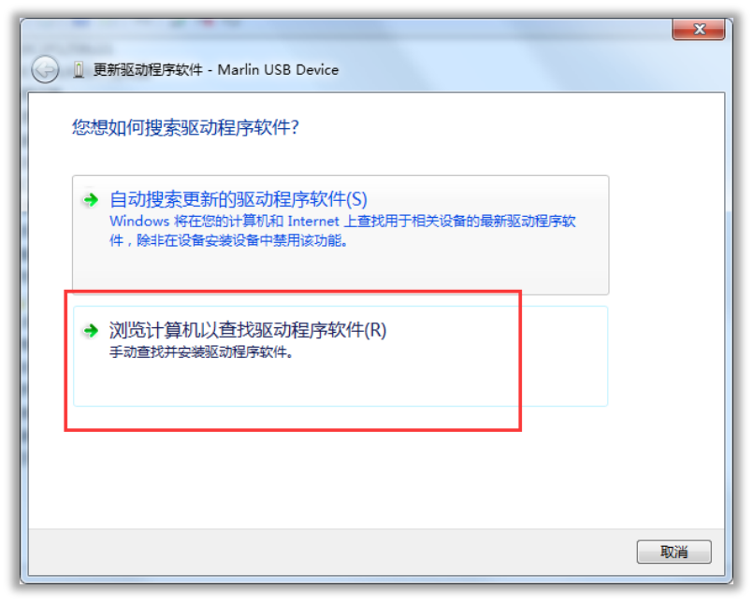
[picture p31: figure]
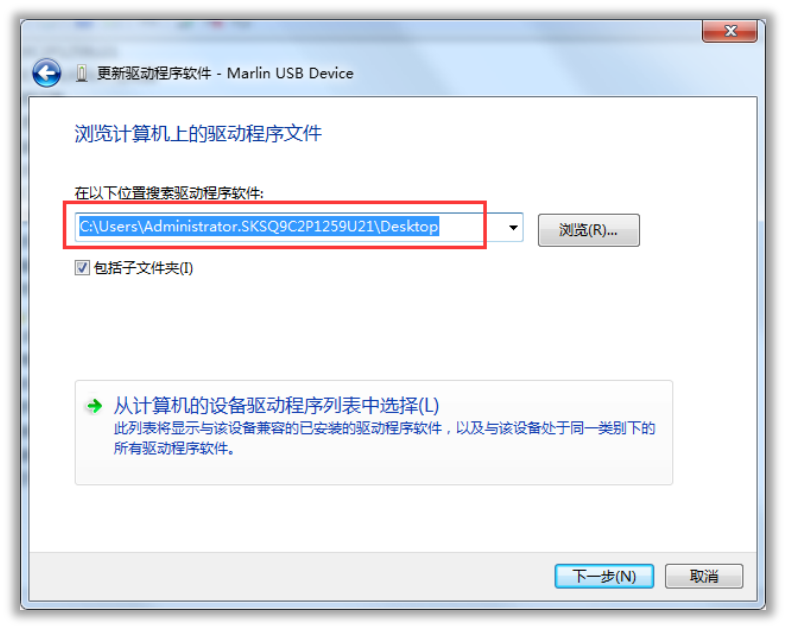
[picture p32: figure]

BIGTREETECH SKR V1.3 guide 2019 – V1 by Jupa Creations Page 11

Select the path as the directory where the lpc176x_usb_driver.inf driver is located. We copied it to the desktop before, so select the desktop location: C:\Users\(Users Name)\Desktop and click Next. Check with the below picture.

If you have firewall alerts, choose to always install this driver software.

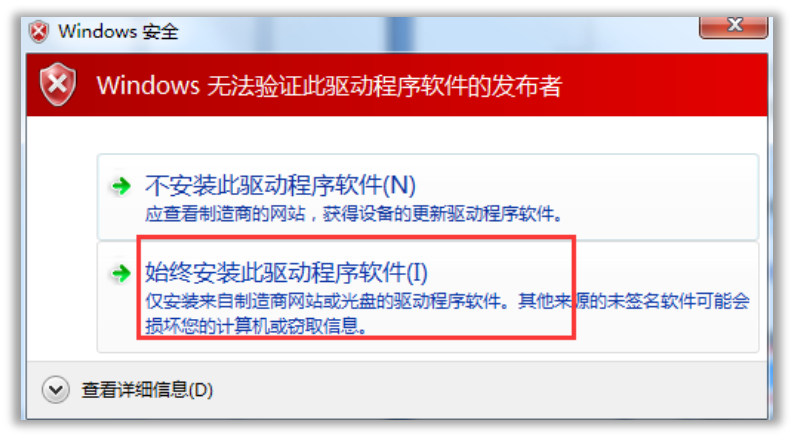
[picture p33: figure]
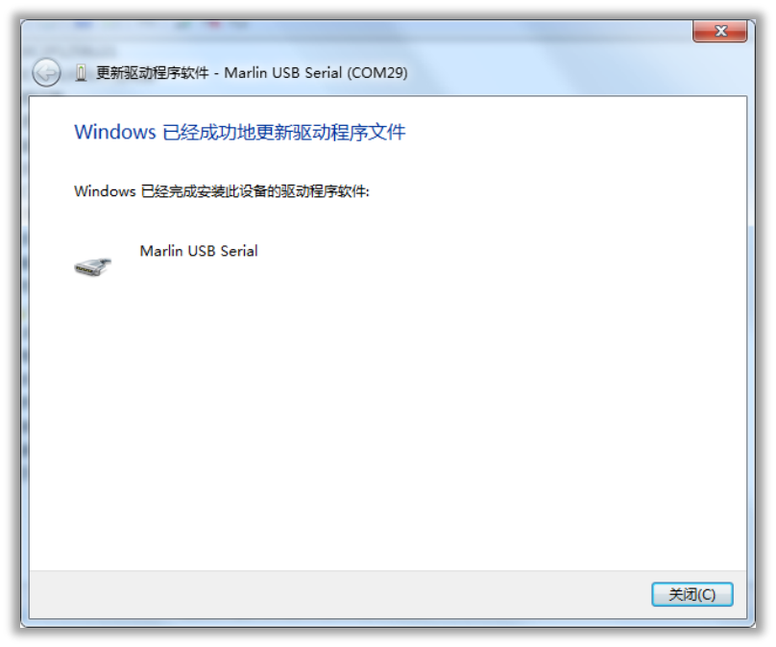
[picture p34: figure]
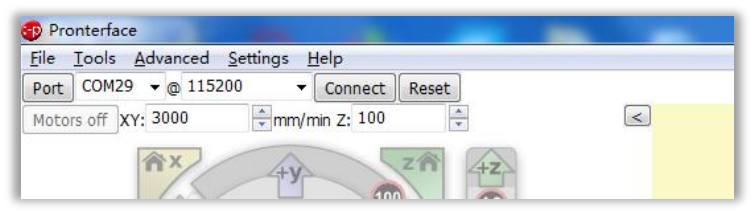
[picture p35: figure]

BIGTREETECH SKR V1.3 guide 2019 – V1 by Jupa Creations Page 12

If the install was successful, then the driver has been selected successfully. Remember the port number.

Open the Printrun/Pronterface online printing software as an example, select your com Port @115200, and then click Connect. Your COM port may be a different number.

On the right, you can see the printer is now online. This means that you have successfully connected to the printer. Now you can use your computer to control the printer

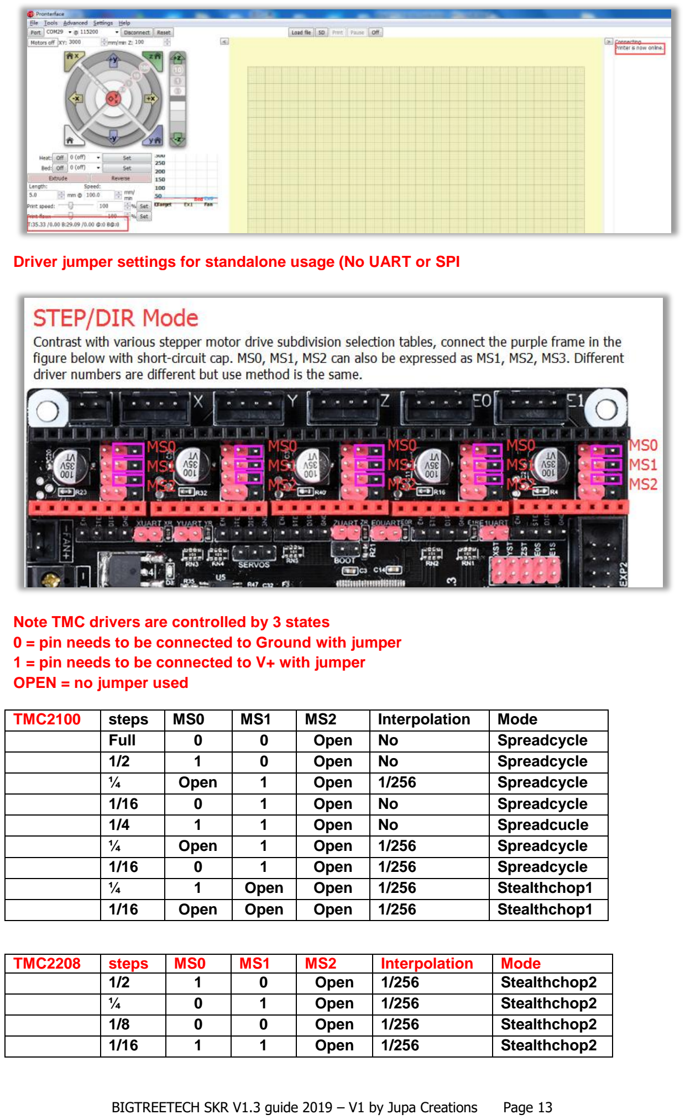
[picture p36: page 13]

BIGTREETECH SKR V1.3 guide 2019 – V1 by Jupa Creations Page 13

Driver jumper settings for standalone usage (No UART or SPI

Note TMC drivers are controlled by 3 states
0 = pin needs to be connected to Ground with jumper 1 = pin needs to be connected to V+ with jumper
OPEN = no jumper used
TMC2100 | steps | MS0 | MS1 | MS2 | Interpolation | Mode
| Full | 0 | 0 | Open | No | Spreadcycle
| 1/2 | 1 | 0 | Open | No | Spreadcycle
| ¼ | Open | 1 | Open | 1/256 | Spreadcycle
| 1/16 | 0 | 1 | Open | No | Spreadcycle
| 1/4 | 1 | 1 | Open | No | Spreadcucle
| ¼ | Open | 1 | Open | 1/256 | Spreadcycle
| 1/16 | 0 | 1 | Open | 1/256 | Spreadcycle
| ¼ | 1 | Open | Open | 1/256 | Stealthchop1
| 1/16 | Open | Open | Open | 1/256 | Stealthchop1
TMC2208 | steps | MS0 | MS1 | MS2 | Interpolation | Mode
| 1/2 | 1 | 0 | Open | 1/256 | Stealthchop2
| ¼ | 0 | 1 | Open | 1/256 | Stealthchop2
| 1/8 | 0 | 0 | Open | 1/256 | Stealthchop2
| 1/16 | 1 | 1 | Open | 1/256 | Stealthchop2

BIGTREETECH SKR V1.3 guide 2019 – V1 by Jupa Creations | Page 14
TMC2130 | steps | MS0 | MS1 | MS2 | Interpolation | Mode
| Full | 0 | 0 | Open | No | Spreadcycle
| ½ | 1 | 0 | Open | No | Spreadcycle
| ½ | Open | 1 | Open | 1/256 | Spreadcycle
| ¼ | 0 | 1 | Open | No | Spreadcycle
| 1/16 | 1 | 1 | Open | No | Spreadcycle
| ¼ | Open | 1 | Open | 1/256 | Spreadcycle
| 1/16 | 0 | Open | Open | 1/256 | Spreadcycle
| ¼ | 1 | Open | Open | 1/256 | Stealthchop1
| 1/16 | Open | Open | Open | 1/256 | Stealthchop1
A4988 | steps | MS0 | MS1 | MS2 | Interpolation | Mode
| Full | 0 | 0 | 0 | No | None
| ½ | 1 | 0 | 0 | No | None
| ¼ | 0 | 1 | 0 | No | None
| 1/8 | 0 | 1 | 0 | No | None
| 1/16 | 1 | 1 | 0 | No | None
DRV8825 | steps | MS0 | MS1 | MS2 | Interpolation | Mode
| Full | 0 | 0 | 0 | No | None
| ½ | 1 | 0 | 0 | No | None
| ¼ | 0 | 1 | 0 | No | None
| 1/8 | 1 | 1 | 0 | No | None
| 1/16 | 0 | 0 | 1 | No | None
| 1/32 | 1 | 1 | 1 | No | None
ST820 | steps | MS0 | MS1 | MS2 | Interpolation | Mode
| Full | 0 | 0 | 0 | No | None
| ½ | 0 | 0 | 1 | No | None
| ¼ | 1 | 0 | 0 | No | None
| 1/8 | 0 | 1 | 1 | No | None
| 1/16 | 1 | 0 | 0 | No | None
| 1/32 | 1 | 0 | 1 | No | None
| 1/128 | 1 | 1 | 0 | No | None
| 1/256 | 1 | 1 | 1 | No | None
LV8729 | Steps | MS0 | MS1 | MS2 | Interpolation | Mode
| Full | 0 | 0 | 0 | No | None
| ½ | 0 | 0 | 1 | No | None
| ¼ | 1 | 0 | 0 | No | None
| 1/8 | 0 | 1 | 1 | No | None
| 1/16 | 1 | 0 | 0 | No | None
| 1/32 | 1 | 0 | 1 | No | None
| 1/64 | 1 | 1 | 0 | No | None
| 1/128 | 1 | 1 | 1 | No | None

BIGTREETECH SKR V1.3 guide 2019 – V1 by Jupa Creations Page 15

Windows 10: Disable Signed Driver Enforcement

How can I install drivers that are not digitally signed?

Windows 10 enforces driver signatures by default. This can be disabled to install drivers that are not digitally signed. Use the following steps to disable driver signature enforcement.

1. Click the Start menu and select Settings.
2. Click Update and Security.
3. Click on Recovery.
4. Click Restart now under Advanced Startup.
5. Click Troubleshoot.
6. Click Advanced options.
7. Click Startup Settings.
8. Click on Restart.
9. On the Startup Settings screen press 7 or F7 to disable driver signature enforcement.

Your computer will restart and you will be able to install non-digitally signed drivers. If you restart your computer again the driver signature enforcement will be re-enabled.

If you are the creator of part of this document and you like your content to be removed please report.

This document is not created by BIGTREETECH!

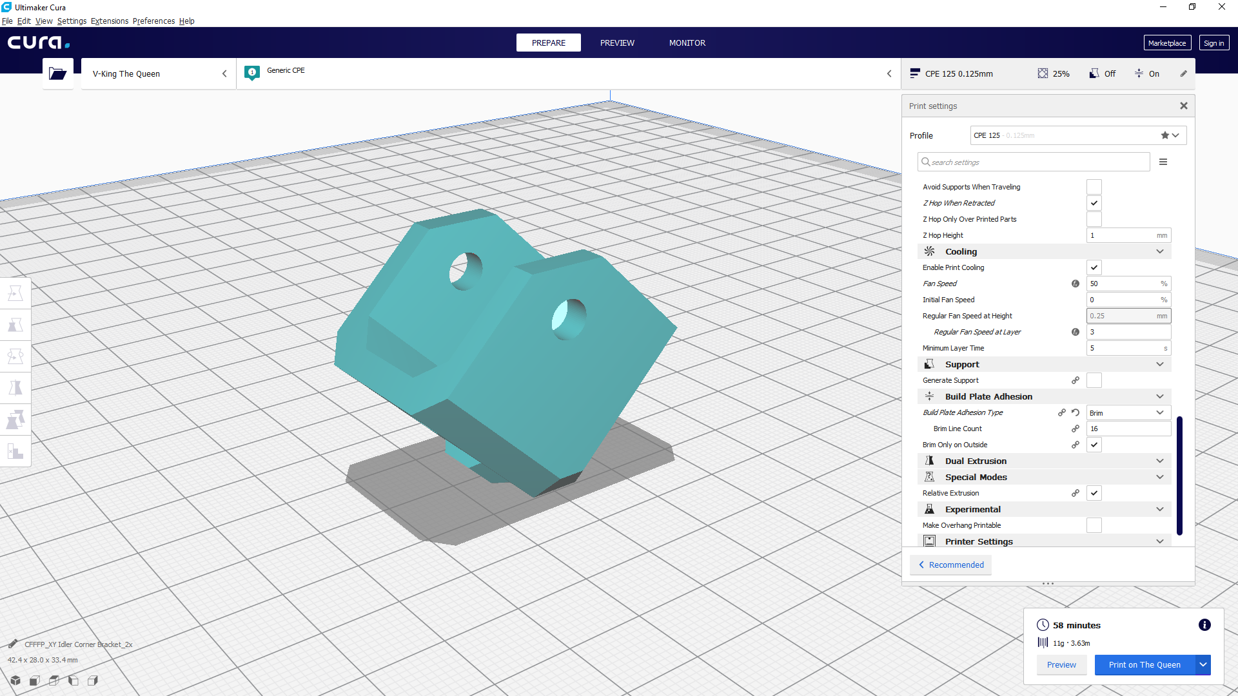
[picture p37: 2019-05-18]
Part Print Files/PrintHelp/XY Idler Corner Bracket_2x.png

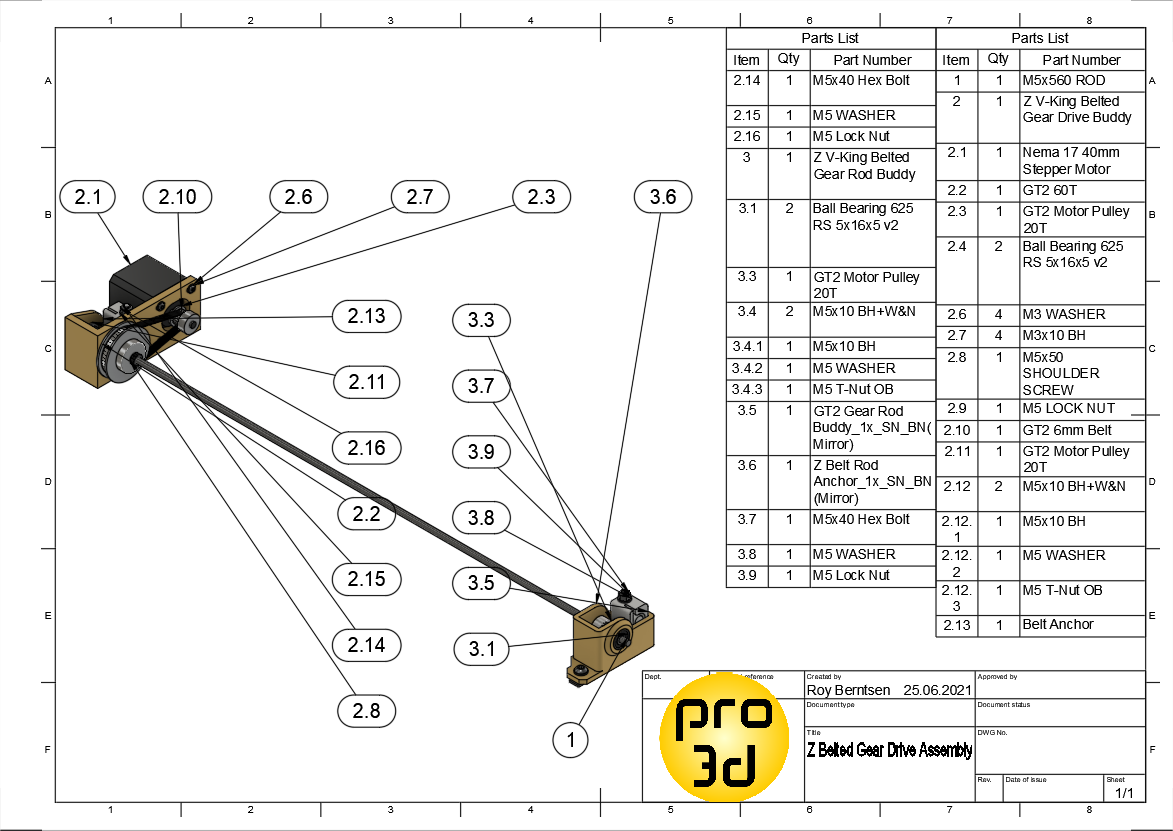
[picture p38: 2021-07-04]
Document Library/Drawings/Z Belted Gear Drive Assembly.png

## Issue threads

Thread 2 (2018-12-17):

X EndStop Bracket has aligment issue

kursatu, 2018-12-17:
There is a single hole so any adjustment is not possible. I had to extend the
5mm opening downward to align it with the flag. Otherwise, it did not work.
The Y end stop bracket has a solution for it, a wider 5mm slit.
PS: Though that GitHub is a better place to report issues, than the FB group.
which is better suited for build discussions.

RoyBerntsenDesign, 2018-12-17:
Hi and thanks for the feedback. This is very important feedback and I
wonder if you have chosen the wrong flag for this part. It is two flags for
two different brackets. Can you tell me what bracket you have?

Best regards/Vennlig hilsen
Roy Berntsen
M.Sc. Design Engineer
Tel: +47 928 26 012
E-mail: roy@pro3d.no
Web: www.pro3d.no

On Mon, Dec 17, 2018 at 6:28 AM Kursat Uvez <notifications@github.com>
wrote:

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

kursatu, 2018-12-18:
Attaching pictures. I've checked with the assembly pdf's drawings
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

RoyBerntsenDesign, 2018-12-18:
Hi again. So you are using the V2 endstop bracket and flag. Those should
sit on the backside of the carrier and not in the front like you have here
- My drawing is old and not right I am sorry. Thanks for pointing that out

This means that the flag should fit better but I also made a change to it
so you can adjust it better

You can find the iterated flag here:
https://github.com/RoyBerntsenDesign/V-King/tree/master/Part%20Print%20Files/XYZ%20Discontinued%20Files

[image: image.png]
Best regards/Vennlig hilsen
Roy Berntsen
M.Sc. Design Engineer
Tel: +47 928 26 012
E-mail: roy@pro3d.no
Web: www.pro3d.no

On Tue, Dec 18, 2018 at 7:02 AM Kursat Uvez <notifications@github.com>
wrote:

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

RoyBerntsenDesign, 2018-12-18:
If you want to upgrade you can add the new endstop bracket and flag for
also bowden support

[image: image.png]
Best regards/Vennlig hilsen
Roy Berntsen
M.Sc. Design Engineer
Tel: +47 928 26 012
E-mail: roy@pro3d.no
Web: www.pro3d.no

On Tue, Dec 18, 2018 at 7:02 AM Kursat Uvez <notifications@github.com>
wrote:

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

kursatu, 2018-12-19:
I've printed the new bracket and end-stop. I'll let you know how well it works when I install it. They looked fine. I see the new bracket in the Fusion360 viewer. It is way better than the pdf's can be outdated easily.

kursatu, 2018-12-20:
It is aligned and works fine. Enjoy the coffee and thanks for the great work.

Closed 2018-12-20.

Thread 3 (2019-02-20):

Wrong bolt size on Y carrier to XY idler ASY in drawings and in BoM

martinroger, 2019-02-20:
The bolts in the drawing "Y-slider drawing" #12 that join the Y carriers to their respective XY idlers is indicated as M4x10, and in the most recent online assembly they are actually M5x14. The BoM does not list any M5x14, but does mention some M5x12. Unfortunately the M5x12 can barely catch one thread of the T-nut on the other side.

The correct size should be M5x14, Qty 4 minimum in the BOM. M5x16 might also work, but it is unverified.

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

RoyBerntsenDesign, 2019-02-22:
Thanks for pointing this out. The brackets was redesignen and I never got
to change the bom... I will do  that this weekend

Best regards/Vennlig hilsen
Roy Berntsen
M.Sc. Design Engineer
Tel: +47 928 26 012
E-mail: roy@pro3d.no
Web: www.pro3d.no

On Wed, Feb 20, 2019 at 11:24 PM Martin ROGER <notifications@github.com>
wrote:

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

RoyBerntsenDesign, 2019-03-01:
Updated the BOM with M5x14

Closed 2019-03-01.

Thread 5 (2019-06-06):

Step Files are not updated to new files. X idlers are still with builtin spacer

coilheaddesigns, 2019-06-06:

RoyBerntsenDesign, 2019-11-19:
I removed all the step files. All parts can now be downloaded from a360

jlipavsky, 2019-11-19:
how do we access them on a360?

RoyBerntsenDesign, 2019-11-20:
You just click the link in the Readme file

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

Closed 2019-06-07.

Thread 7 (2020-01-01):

V-King Belted Z axis not moving up uniformly

stoky996, 2020-01-01:
after assembling my v-king i noticed that when testing my z axis it was not moving up correctly causing bed leveling to fail when the bed moved upwards the right side moved up faster then the left causing it to become slanted and when moving downwards the left hand side slants tightening the left causes the right side to resume it's behavior i will upload a video tomorrow i should say that the other side is fine and does not move. i will upload a video tomorrow got other stuff to do and will be at work tomorrow.

RoyBerntsenDesign, 2020-01-01:
Thank you for the feedback. Can you go to discord or messenger support chat
to solve this is more easy to help you. Also the Facebook group can help

Messenger:
Discord: https://discord.gg/MRgjAqT
FB: https://www.facebook.com/groups/viking3d/

Best regards/Vennlig hilsen
Roy Berntsen
M.Sc. Design Engineer
Tel: +47 928 26 012
E-mail: roy@pro3d.no
Web: www.pro3d.no

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

stoky996, 2020-01-01:
Cheers I have joined the Facebook group and continuing it from there thanks for responding anyhow.

Regards jesse

Closed 2020-01-01.

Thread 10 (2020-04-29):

M5 80D copper washer in assembly drawings

cscott, 2020-04-29:
This is presumably the "M5 GT2 Idler Shim" from the BOM?  What are the source and/or dimensions of this?

cscott, 2020-04-29:
In the "Base Mechanical Kit" from makersupplies.sk this seems to be what is listed as "M5 Mini Precision Shim 8x5x1 (25)".  So something like https://www.aliexpress.com/item/32812003364.html ?

RoyBerntsenDesign, 2020-04-29:
The best option shim is 1mm thick 5 bore and 6 or 7mm outer diameter. The
stock option has been 5x8x1 (boreXodXthick) and these should be ok to use
as well but someone noted the outer dia could be little big for some
bearings

ons. 29. apr. 2020, 07:59 skrev C. Scott Ananian <notifications@github.com>:

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

cscott, 2020-04-29:
It seems that M5x7x0.5 shims are what's readily available on aliexpress, etc.  Presumably two of these could be used instead of the 5x8x1.

RoyBerntsenDesign, 2020-04-30:
Yes those are perfect

On Thu, Apr 30, 2020, 00:28 C. Scott Ananian <notifications@github.com>
wrote:

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

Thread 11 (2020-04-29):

Assembly drawing for the X slider?

cscott, 2020-04-29:
The X slider is missing from the assembly drawings folder.  I expect the reason is because your design was in flux, but it would still be very nice to see at least one example of how that is put together.  For example, to get insight into the BOM needed, and how the belts are secured.

RoyBerntsenDesign, 2020-04-30:
I hope this video can help you
https://youtu.be/YC2f6RIYLkI

On Thu, Apr 30, 2020, 00:30 C. Scott Ananian <notifications@github.com>
wrote:

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

RoyBerntsenDesign, 2020-04-30:
Here's how to secure the belt's. There will be a new carrier out today if
you want the latest and greatest. Take a look at the 3d model

On Thu, Apr 30, 2020, 00:30 C. Scott Ananian <notifications@github.com>
wrote:

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

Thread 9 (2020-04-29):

GT belt width in BOM

cscott, 2020-04-29:
The BOM doesn't say the width or length of the GT belt, and at the links provided both the belt and the idler and motor pulleys are available in a variety of widths.  In the assembly drawing for the "XY Belt Tension Drawing" it says "Use 3mm, 4mm, or 5mm smooth idlers here" -- is that the bore?  I'd assume you'd need to use 5mm to match the M5 bolts.

I'm guessing "20tooth width 6mm bore 5mm without teeth" for the smooth pulley, and "20tooth width 6mm bore 5mm (with teeth)" for the toothed pulley.  For the motor pulley, is the 20 tooth one with a 7mm width for the belt, 15mm overall height, and 5mm bore the correct one?

RoyBerntsenDesign, 2020-04-29:
Hi and thanks for the feedback. This is important info and I will update
the bom soon. I have 20t pulleys and idlers. All 5mm bore yes. Belt is 6mm
wide and I dont remember the length. Let me check if I have this noted

ons. 29. apr. 2020, 07:58 skrev C. Scott Ananian <notifications@github.com>:

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

cscott, 2020-04-29:
By my math, the length of the each XY belt should be the same as the circumference of the XY frame.  It would be interesting to note how much "extra" was needed for securing it to the X slider, so that folks building different sizes could get a rough idea of how much extra to leave.

RoyBerntsenDesign, 2020-04-30:
So i just measured and get about 180 cm and suggest 200cm for each xy belt.
I get 150 cm for each z drive. This means 700cm as a minimum in total

On Thu, Apr 30, 2020, 00:27 C. Scott Ananian <notifications@github.com>
wrote:

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

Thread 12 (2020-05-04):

Stop printing

CatalinCambosie, 2020-05-04:
Dear Roy, I found out about your 3d printer concept and I liked it very much. So, I bought one, already built. Unfortunately, I encountered an issue while printing, all the time after about 30 minutes of printing. It looks like a heat  bed temperature issue, also the led on mosfet stops. When restart, it's ok for the moment. I checked the 2 pin connector of the termistor. Same issue. Strange is because it stops after about 30 minutes all the time. The board is MKS Gen L.  Could be only a termistor issue?
Please help me with your expert advise.

Best regards,
 Catalin

RoyBerntsenDesign, 2020-05-05:
This I can't help with I am sorry. Please try ask in the FB group

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

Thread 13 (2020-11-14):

Z motor offset

kyemacdonald, 2020-11-14:
Morning Roy,

I'm in the process of building one of your machines but have a slight fitment issue.  My worm gear doesn't engage properly as the spacing between the gears is too large.  I end up with a lot of slop.

Would it be possible to get an editable version of the Z motor mount so that I can move the motor mount holes?  Or alternativley an STL with those holes adjust to allow the motor to move up / down?

Thanks

Kye

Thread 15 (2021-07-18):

BOM Missing Frame and Wheel Parts

caleb, 2021-07-18:
Hi guys,

The BOM is missing the frame and wheel parts that the old v1 BOM used to have.

Is this an oversight, or should I create a PR with an updated XLSX file? The frame and wheel parts are included in the link to the MakerSupplies bundle, but the spreadsheet doesn’t list them.

Thanks!

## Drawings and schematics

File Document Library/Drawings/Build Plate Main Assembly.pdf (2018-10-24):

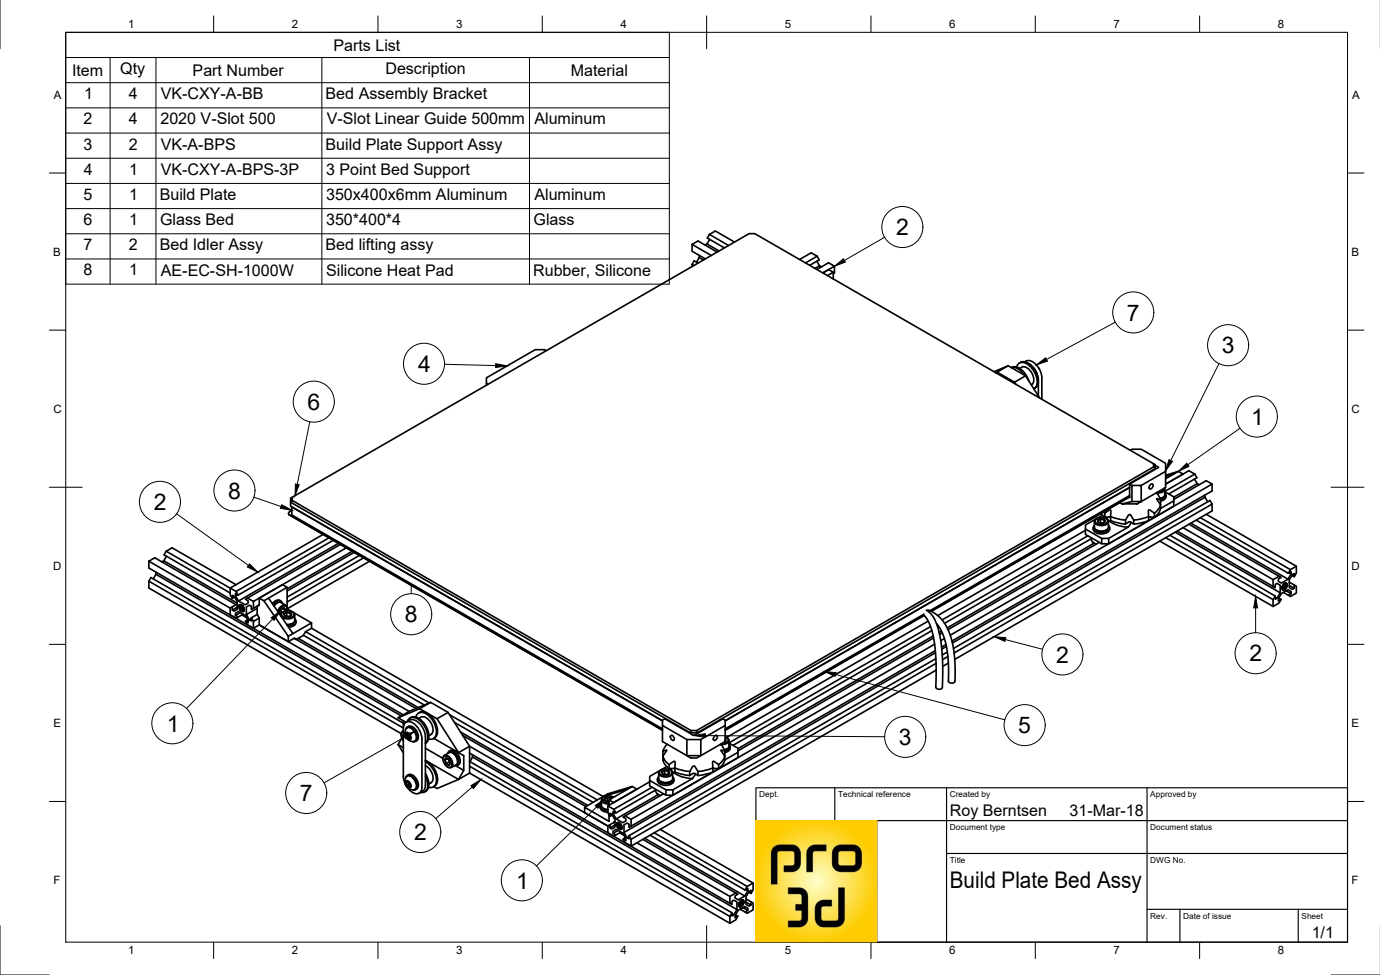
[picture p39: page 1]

Parts List

Item | Qty | Part Number | Description | Material
1 | 4 | VK-CXY-A-BB | Bed Assembly Bracket
2 | 4 | 2020 V-Slot 500 | V-Slot Linear Guide 500mm | Aluminum
3 | 2 | VK-A-BPS | Build Plate Support Assy
4 | 1 | VK-CXY-A-BPS-3P | 3 Point Bed Support
5 | 1 | Build Plate | 350x400x6mm Aluminum | Aluminum
6 | 1 | Glass Bed | 350*400*4 | Glass
7 | 2 | Bed Idler Assy | Bed lifting assy
8 | 1 | AE-EC-SH-1000W | Silicone Heat Pad | Rubber, Silicone

Dept. | Technical reference | Created by Roy Berntsen 31-Mar-18 | Approved by

Document type | Document status

Title Build Plate Bed Assy | DWG No.

Rev. | Date of issue | Sheet 1/1

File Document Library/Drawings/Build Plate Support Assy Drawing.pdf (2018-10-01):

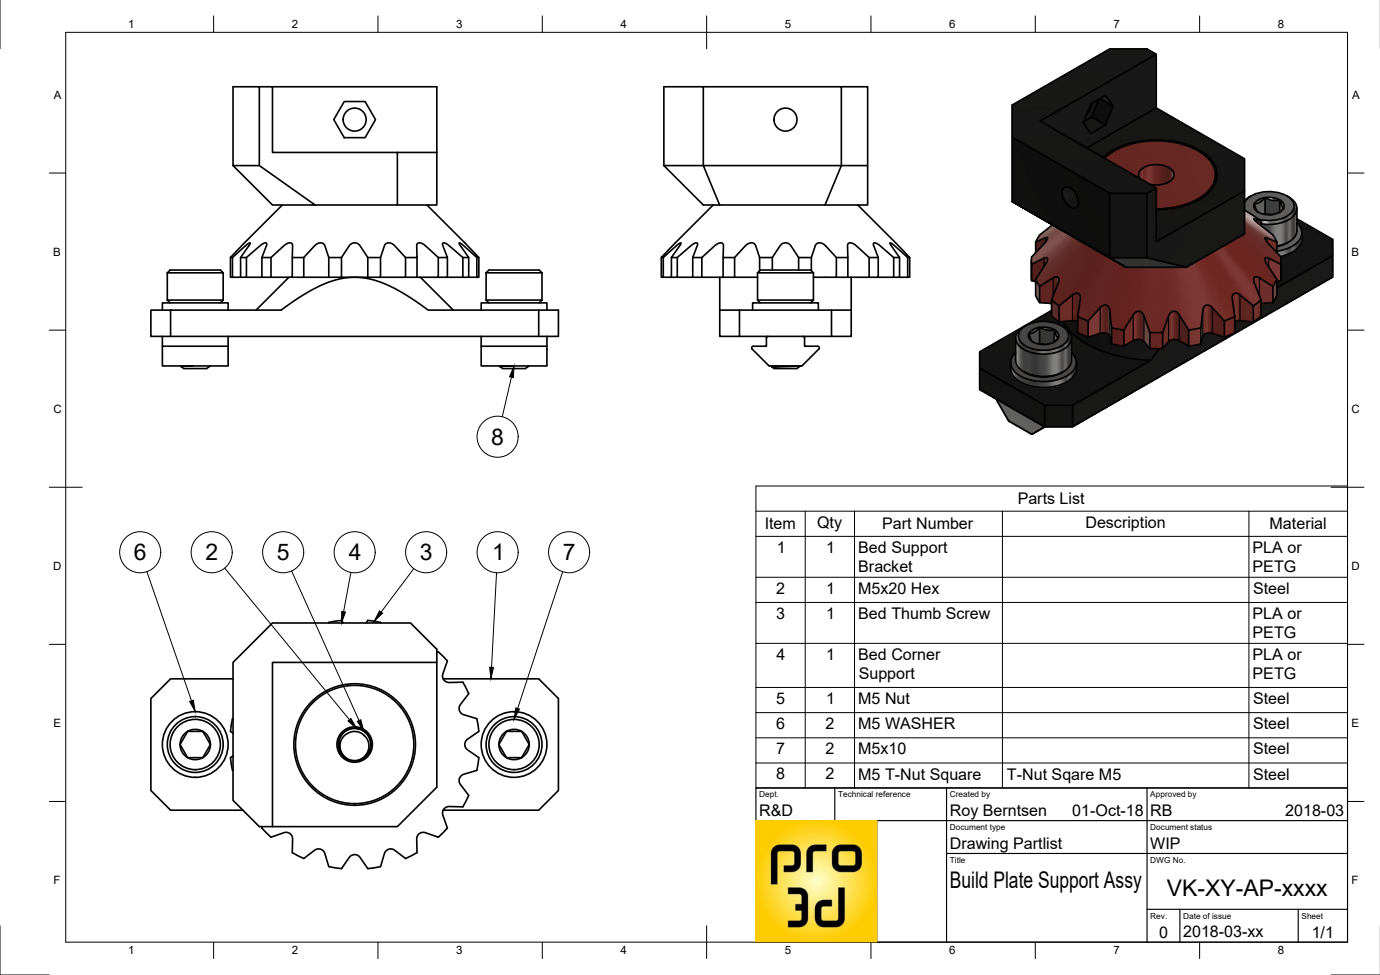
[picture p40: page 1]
Parts List

Item | Qty | Part Number | Description | Material
1 | 1 | Bed Support Bracket | | PLA or PETG

2 | 1 | M5x20 Hex | | Steel
3 4 | 1 1 | Bed Thumb Screw Bed Corner Support | | PLA or PETG

5 | 1 | M5 Nut | | Steel
6 | 2 | M5 WASHER | | Steel
7 | 2 | M5x10 | | Steel
8 | 2 | M5 T-Nut Square | T-Nut Sqare M5 | Steel

Dept. R&D | Technical reference | Created by Roy Berntsen 01-Oct-18 | Approved by RB 2018-03

Document type Drawing Partlist | Document status WIP

Title | DWG No. VK-XY-AP-xxxx Build Plate Support Assy

Rev. 0 | Date of issue 2018-03-xx | Sheet 1/1

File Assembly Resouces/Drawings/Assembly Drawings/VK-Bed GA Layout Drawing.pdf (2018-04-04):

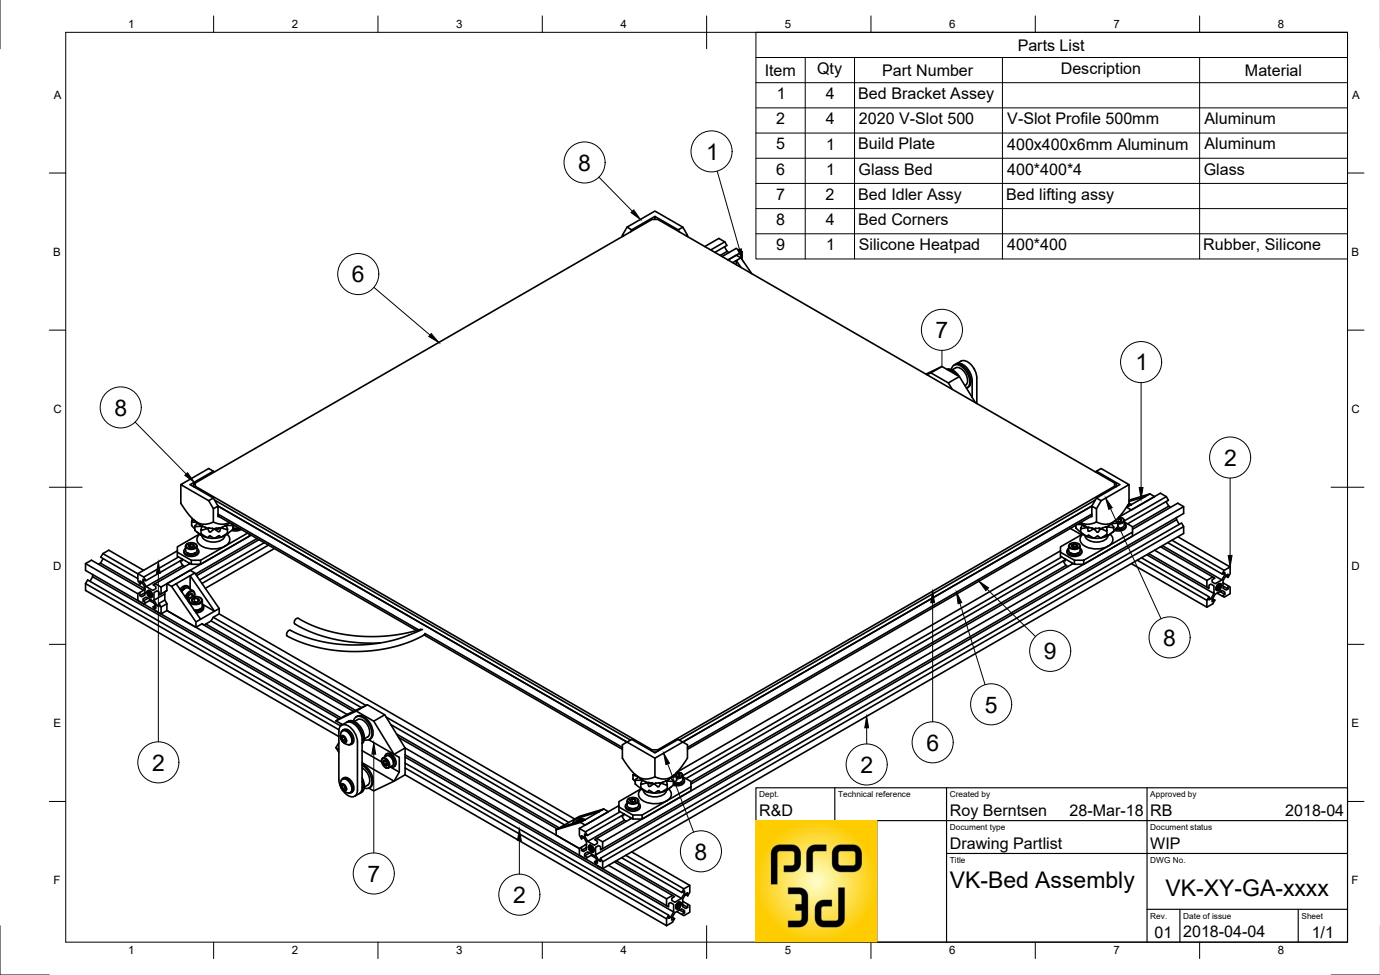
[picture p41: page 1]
Parts List

Item | Qty | Part Number | Description | Material
1 | 4 | Bed Bracket Assey
2 | 4 | 2020 V-Slot 500 | V-Slot Profile 500mm | Aluminum
5 | 1 | Build Plate | 400x400x6mm Aluminum | Aluminum
6 | 1 | Glass Bed | 400*400*4 | Glass
7 | 2 | Bed Idler Assy | Bed lifting assy
8 | 4 | Bed Corners
9 | 1 | Silicone Heatpad | 400*400 | Rubber, Silicone

Dept. R&D | Technical reference | Created by Roy Berntsen 28-Mar-18 | Approved by RB 2018-04

Document type Drawing Partlist | Document status WIP

Title | DWG No. VK-XY-GA-xxxx VK-Bed Assembly

Rev. 01 | Date of issue 2018-04-04 | Sheet 1/1

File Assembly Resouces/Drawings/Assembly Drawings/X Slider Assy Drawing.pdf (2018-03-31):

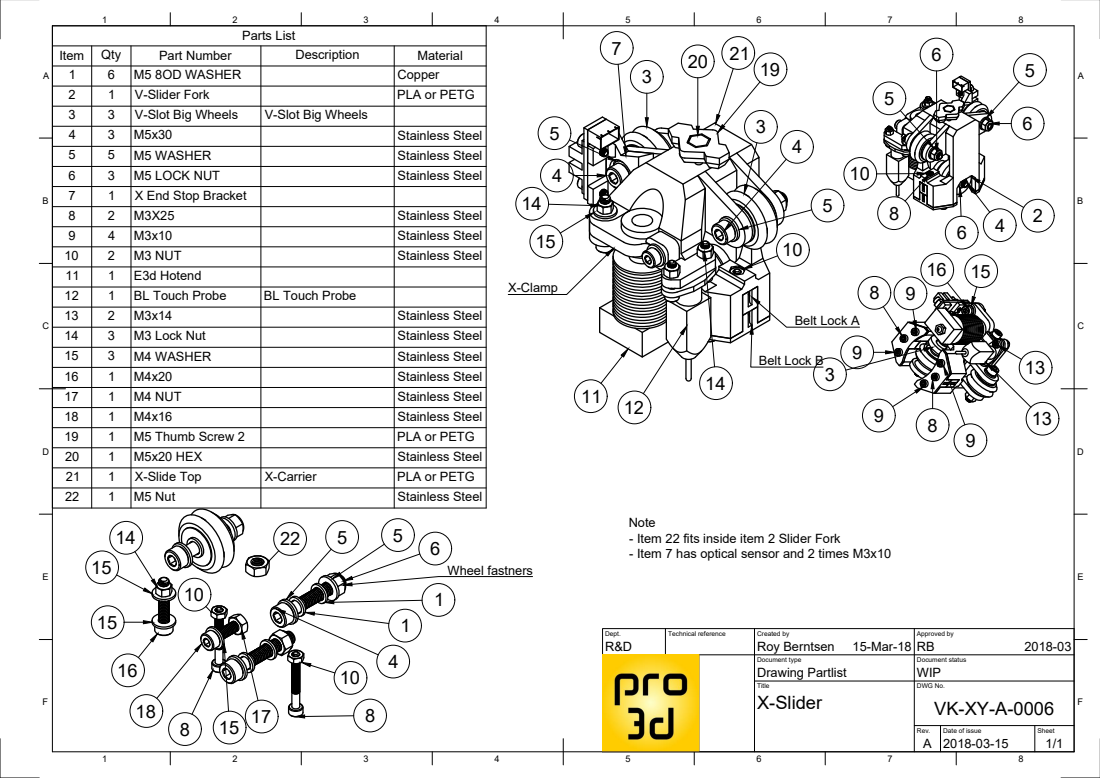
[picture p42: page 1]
Belt Lock A; Belt Lock B; Wheel fastners

Parts List

Item | Qty | Part Number | Description | Material
1 | 6 | M5 8OD WASHER | | Copper
2 | 1 | V-Slider Fork | | PLA or PETG
3 | 3 | V-Slot Big Wheels | V-Slot Big Wheels
4 | 3 | M5x30 | | Stainless Steel
5 | 5 | M5 WASHER | | Stainless Steel
6 | 3 | M5 LOCK NUT | | Stainless Steel
7 | 1 | X End Stop Bracket
8 | 2 | M3X25 | | Stainless Steel
9 | 4 | M3x10 | | Stainless Steel
10 | 2 | M3 NUT | | Stainless Steel
11 | 1 | E3d Hotend
12 | 1 | BL Touch Probe | BL Touch Probe
13 | 2 | M3x14 | | Stainless Steel
14 | 3 | M3 Lock Nut | | Stainless Steel
15 | 3 | M4 WASHER | | Stainless Steel
16 | 1 | M4x20 | | Stainless Steel
17 | 1 | M4 NUT | | Stainless Steel
18 | 1 | M4x16 | | Stainless Steel
19 | 1 | M5 Thumb Screw 2 | | PLA or PETG

20 | 1 | M5x20 HEX | | Stainless Steel
21 | 1 | X-Slide Top | X-Carrier | PLA or PETG
22 | 1 | M5 Nut | | Stainless Steel

Note
- Item 22 fits inside item 2 Slider Fork
- Item 7 has optical sensor and 2 times M3x10

Dept. R&D | Technical reference | Created by Roy Berntsen 15-Mar-18 | Approved by RB 2018-03

Document type Drawing Partlist | Document status WIP

Title | DWG No. VK-XY-A-0006 X-Slider

Rev. A | Date of issue 2018-03-15 | Sheet 1/1

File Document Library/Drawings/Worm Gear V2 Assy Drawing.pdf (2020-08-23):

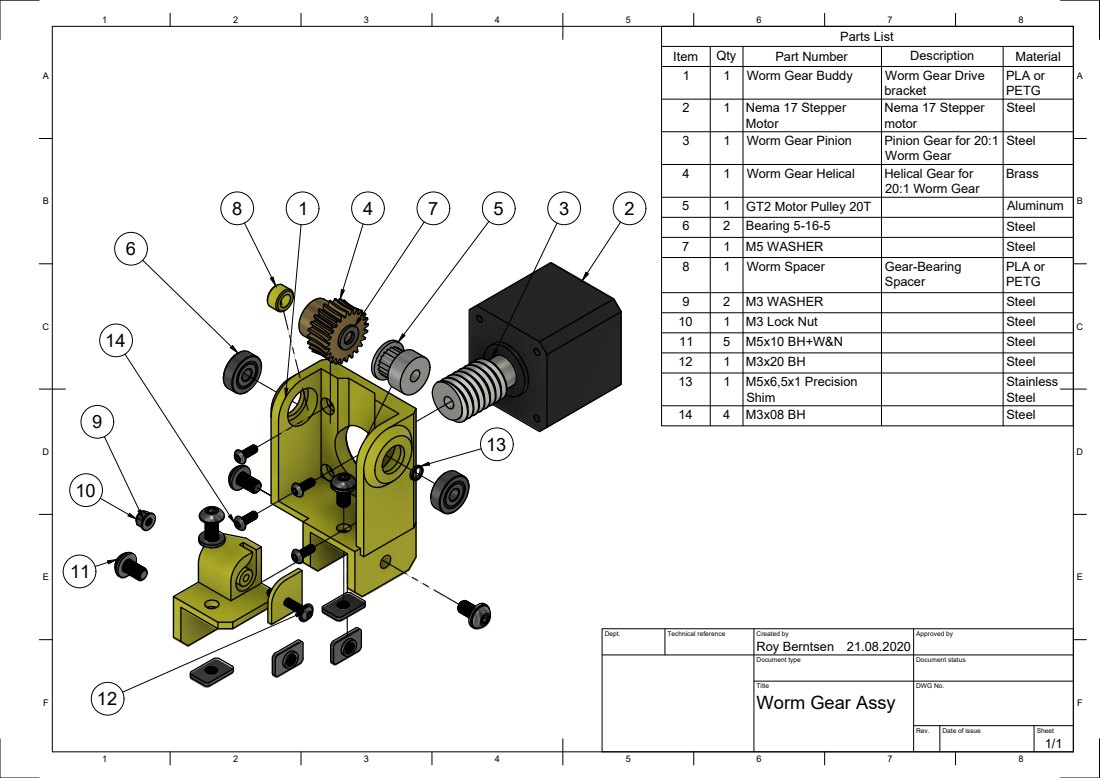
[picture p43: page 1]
Parts List

Item | Qty | Part Number | Description | Material
1 | 1 | Worm Gear Buddy | Worm Gear Drive bracket | PLA or PETG

2 | 1 | Nema 17 Stepper Motor | Nema 17 Stepper motor | Steel

3 | 1 | Worm Gear Pinion | Pinion Gear for 20:1 Worm Gear | Steel

4 | 1 | Worm Gear Helical | Helical Gear for 20:1 Worm Gear | Brass

5 | 1 | GT2 Motor Pulley 20T | | Aluminum
6 | 2 | Bearing 5-16-5 | | Steel
7 | 1 | M5 WASHER | | Steel
8 | 1 | Worm Spacer | Gear-Bearing Spacer | PLA or PETG

9 | 2 | M3 WASHER | | Steel
10 | 1 | M3 Lock Nut | | Steel
11 | 5 | M5x10 BH+W&N | | Steel
12 | 1 | M3x20 BH | | Steel
13 | 1 | M5x6,5x1 Precision Shim | | Stainless Steel

14 | 4 | M3x08 BH | | Steel

Dept. | Technical reference | Created by Roy Berntsen 21.08.2020 | Approved by

Document type | Document status

Title Worm Gear Assy | DWG No.

Rev. | Date of issue | Sheet 1/1

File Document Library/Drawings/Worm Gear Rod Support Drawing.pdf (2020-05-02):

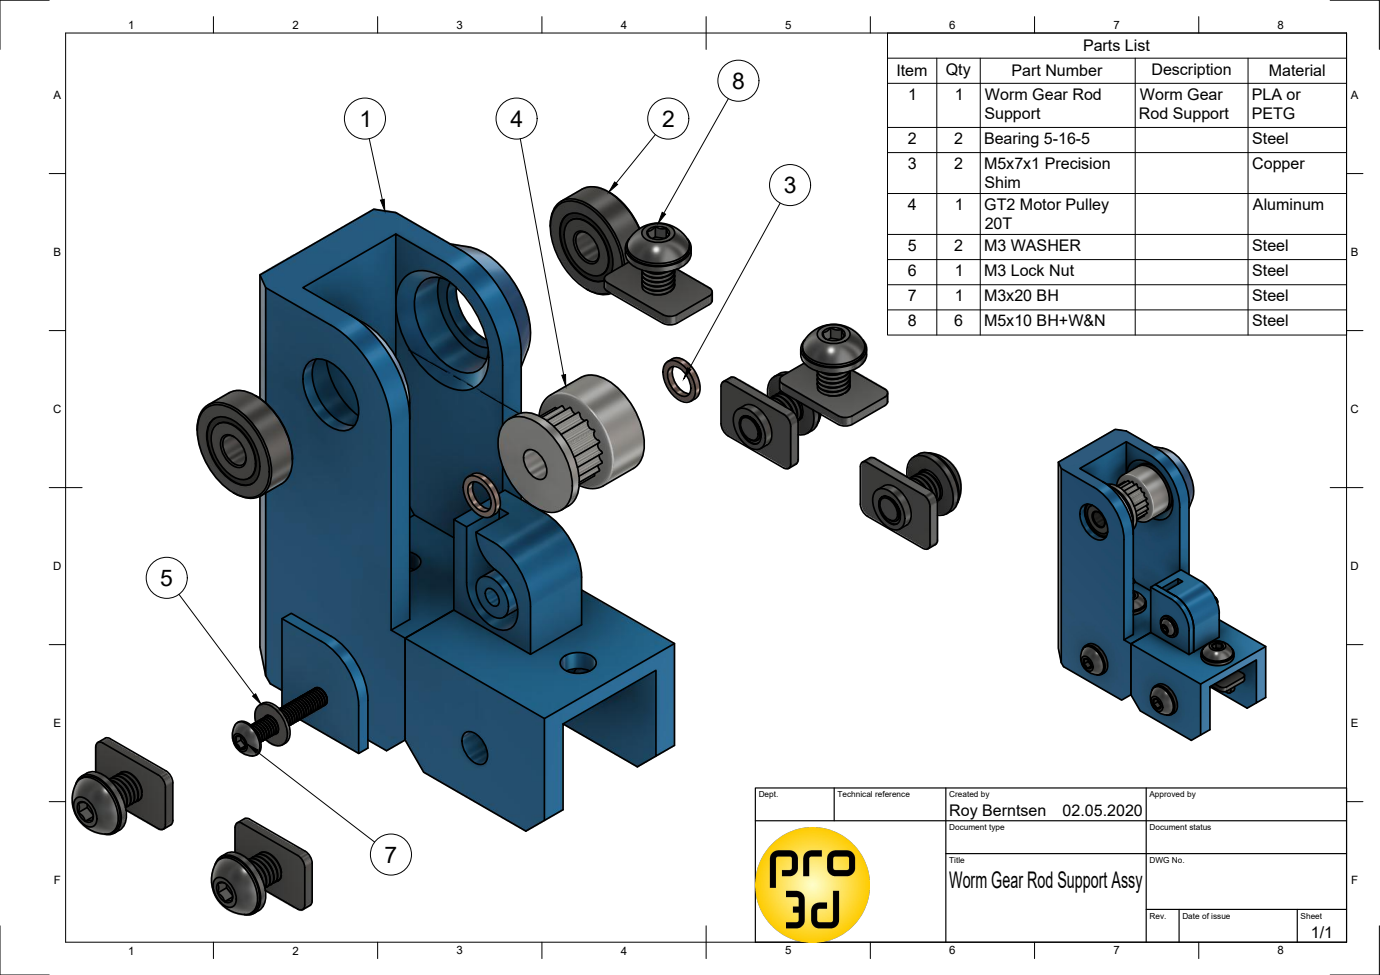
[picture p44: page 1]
Parts List

Item | Qty | Part Number | Description | Material
1 | 1 | Worm Gear Rod Support | Worm Gear Rod Support | PLA or PETG

2 | 2 | Bearing 5-16-5 | | Steel
3 | 2 | M5x7x1 Precision Shim | | Copper

4 | 1 | GT2 Motor Pulley 20T | | Aluminum

5 | 2 | M3 WASHER | | Steel
6 | 1 | M3 Lock Nut | | Steel
7 | 1 | M3x20 BH | | Steel
8 | 6 | M5x10 BH+W&N | | Steel

Dept. | Technical reference | Created by Roy Berntsen 02.05.2020 | Approved by

Document type | Document status

Title Worm Gear Rod Support Assy | DWG No.

Rev. | Date of issue | Sheet 1/1

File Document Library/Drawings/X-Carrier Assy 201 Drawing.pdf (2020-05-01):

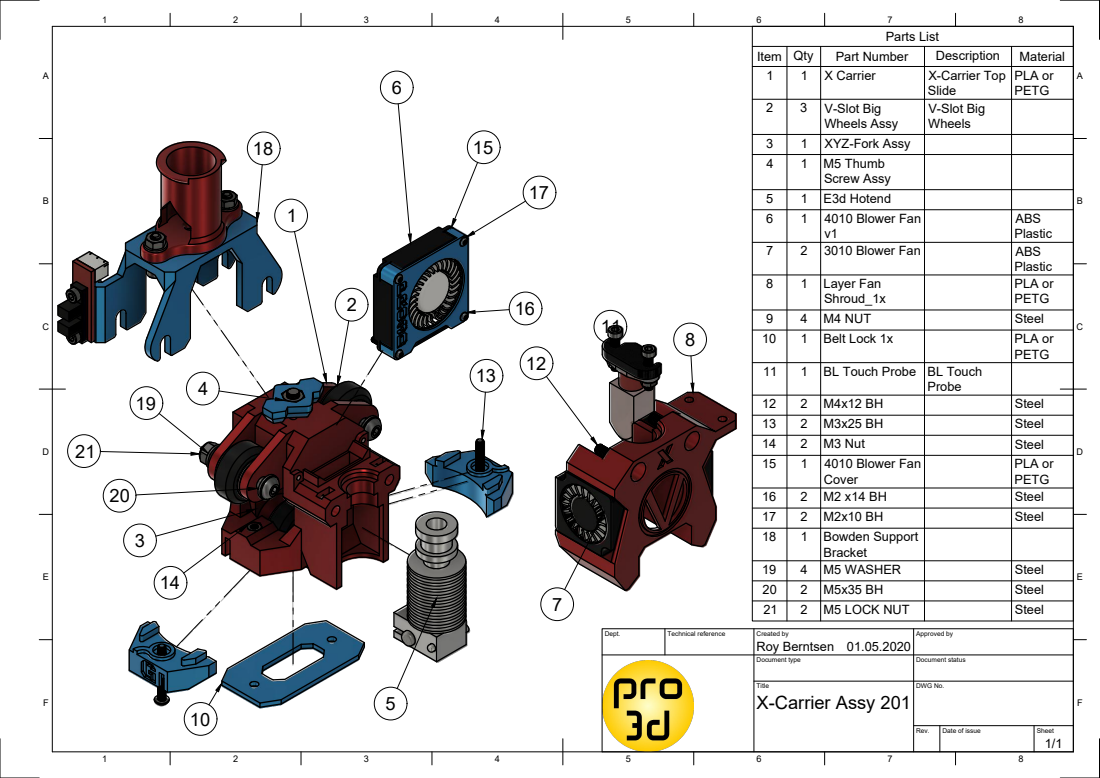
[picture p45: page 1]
8 BCDEF; ABCDEF; Parts List

Item | Qty 1 | X Carrier Part Number | X-Carrier Top Description | Material 1
3 | V-Slot Big | Slide | PLA or PETG 2

Wheels Assy | V-Slot Big

1 1 | M5 Thumb XYZ-Fork Assy 4 | Wheels 3

1 1 | E3d Hotend 6 Screw Assy 5 4010 Blower Fan

2 | 3010 Blower Fan v1 | ABS Plastic 7 ABS

1 | Layer Fan | Plastic 8
4 | M4 NUT Shroud_1x | PLA or PETG 9 Steel

10 | 1 | Belt Lock 1x | | PLA or PETG

11 | 1 | BL Touch Probe | BL Touch Probe

12 | 2 | M4x12 BH | | Steel
13 | 2 | M3x25 BH | | Steel
14 | 2 | M3 Nut | | Steel
15 | 1 | 4010 Blower Fan Cover | | PLA or PETG

16 | 2 | M2 x14 BH | | Steel
17 | 2 | M2x10 BH | | Steel
18 | 1 | Bowden Support Bracket

19 | 4 | M5 WASHER | | Steel
20 | 2 | M5x35 BH | | Steel
21 | 2 | M5 LOCK NUT | | Steel

Dept. | Technical reference | Created by Roy Berntsen 01.05.2020 | Approved by

Document type | Document status

Title X-Carrier Assy 201 | DWG No.

Rev. | Date of issue | Sheet 1/1

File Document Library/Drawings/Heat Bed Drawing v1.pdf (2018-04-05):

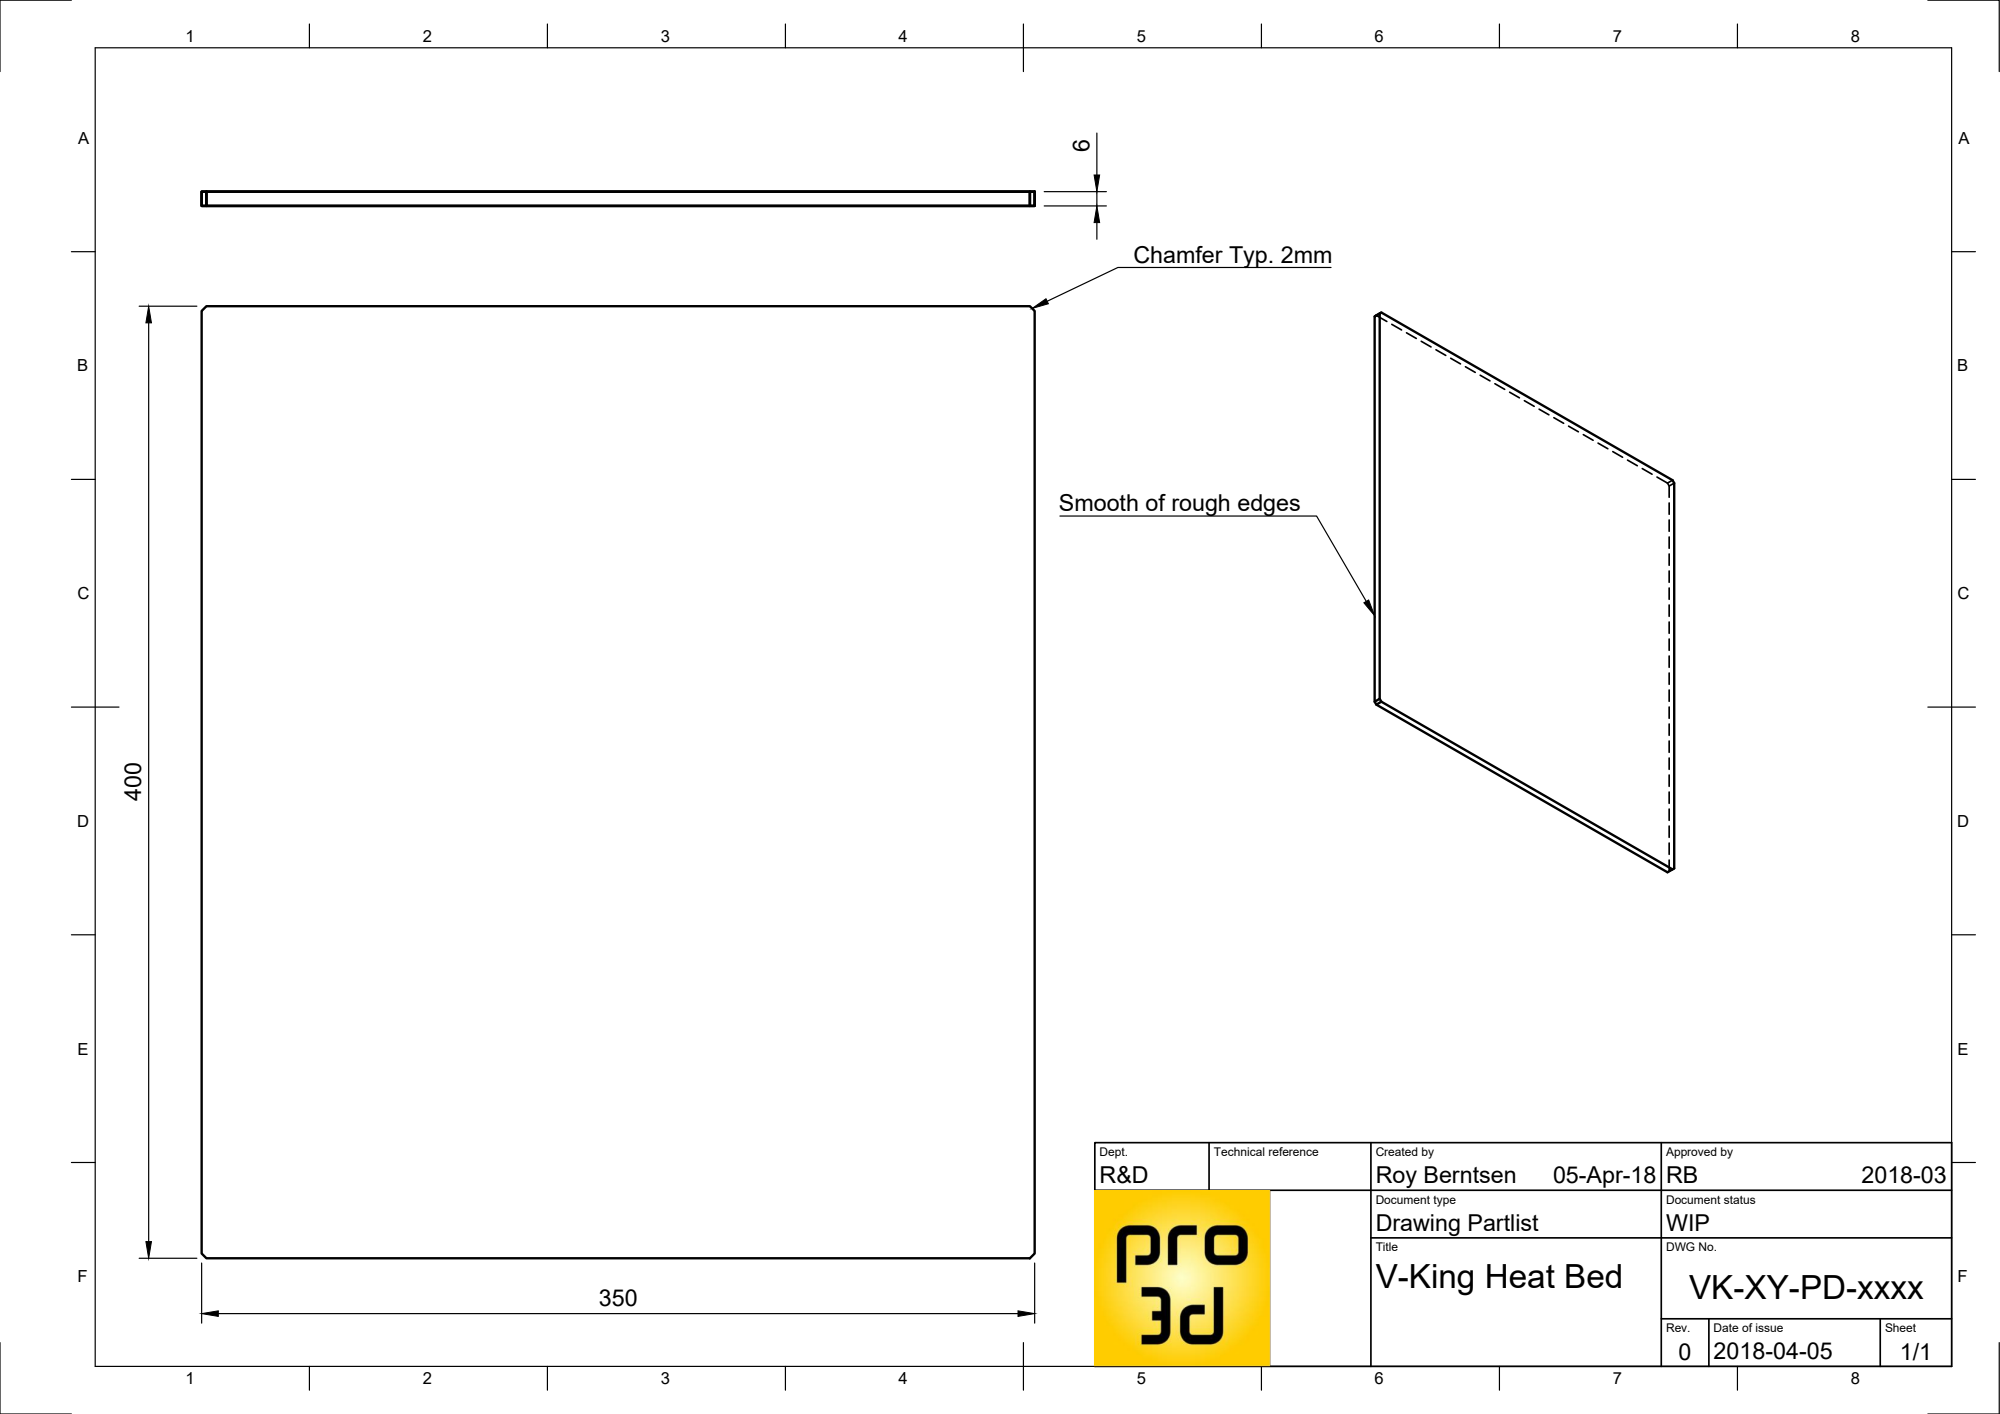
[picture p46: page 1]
Roy Berntsen; Chamfer Typ. 2mm

Smooth of rough edges

Dept. | Technical reference | Created by 05-Apr-18 | Approved by 2018-03

Document type Drawing Partlist | Document status WIP

Title | DWG No. VK-XY-PD-xxxx V-King Heat Bed

Rev. 0 | Date of issue 2018-04-05 | Sheet 1/1

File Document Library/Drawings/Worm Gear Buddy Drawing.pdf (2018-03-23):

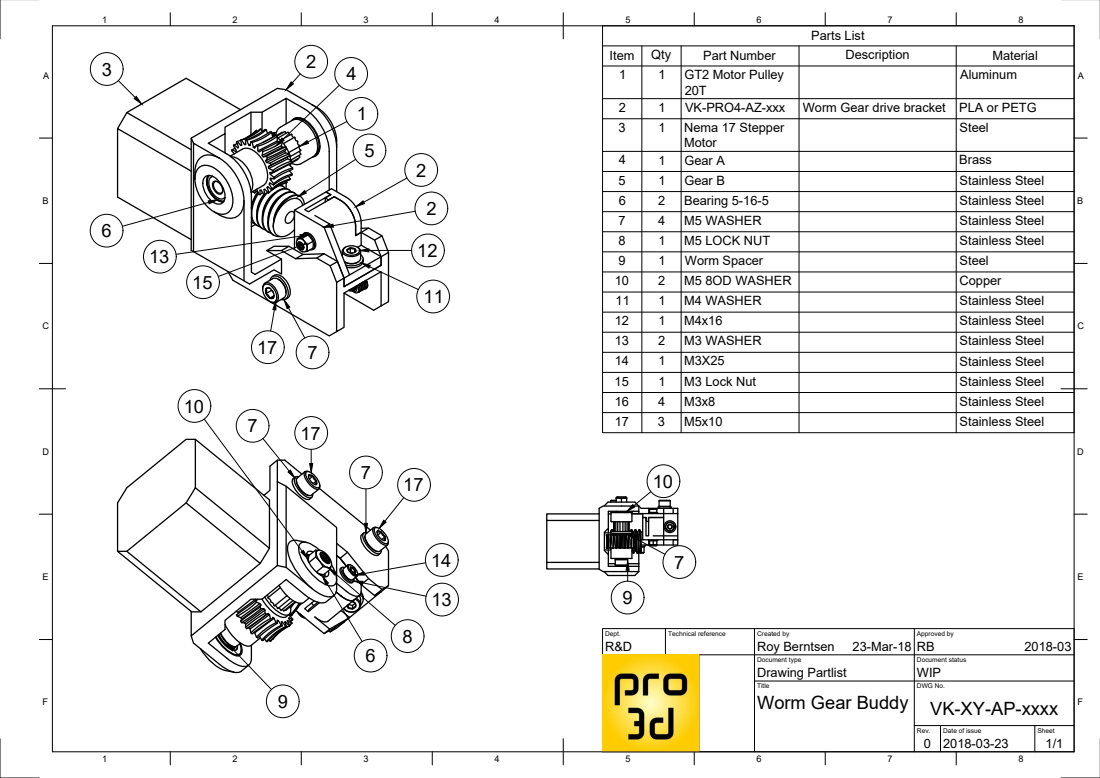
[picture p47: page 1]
8 BCDEF; ABCDEF; Parts List; Stainless Steel 3

Item | Qty 1 | GT2 Motor Pulley Part Number | Description | Material 1
1 1 | Nema 17 Stepper VK-PRO4-AZ-xxx 20T | Worm Gear drive bracket | PLA or PETG 3 Aluminum 2

2 4 1 1 1 1 | M5 WASHER M5 LOCK NUT Bearing 5-16-5 Gear A Gear B Worm Spacer | Brass 5 Steel 4 Stainless Steel 6 Stainless Steel 7 Stainless Steel 8 Stainless Steel 9 Steel

Motor

10 | 2 | M5 8OD WASHER | Copper
11 | 1 | M4 WASHER | Stainless Steel
12 | 1 | M4x16 | Stainless Steel
13 | 2 | M3 WASHER | Stainless Steel
14 | 1 | M3X25 | Stainless Steel
15 | 1 | M3 Lock Nut | Stainless Steel
16 | 4 | M3x8 | Stainless Steel

Dept. R&D | Technical reference | Created by Roy Berntsen 23-Mar-18 | Approved by RB 2018-03

Document type Drawing Partlist | Document status WIP

Title Worm Gear Buddy | DWG No. VK-XY-AP-xxxx

Rev. | Date of issue 2018-03-23 | Sheet 0 1/1

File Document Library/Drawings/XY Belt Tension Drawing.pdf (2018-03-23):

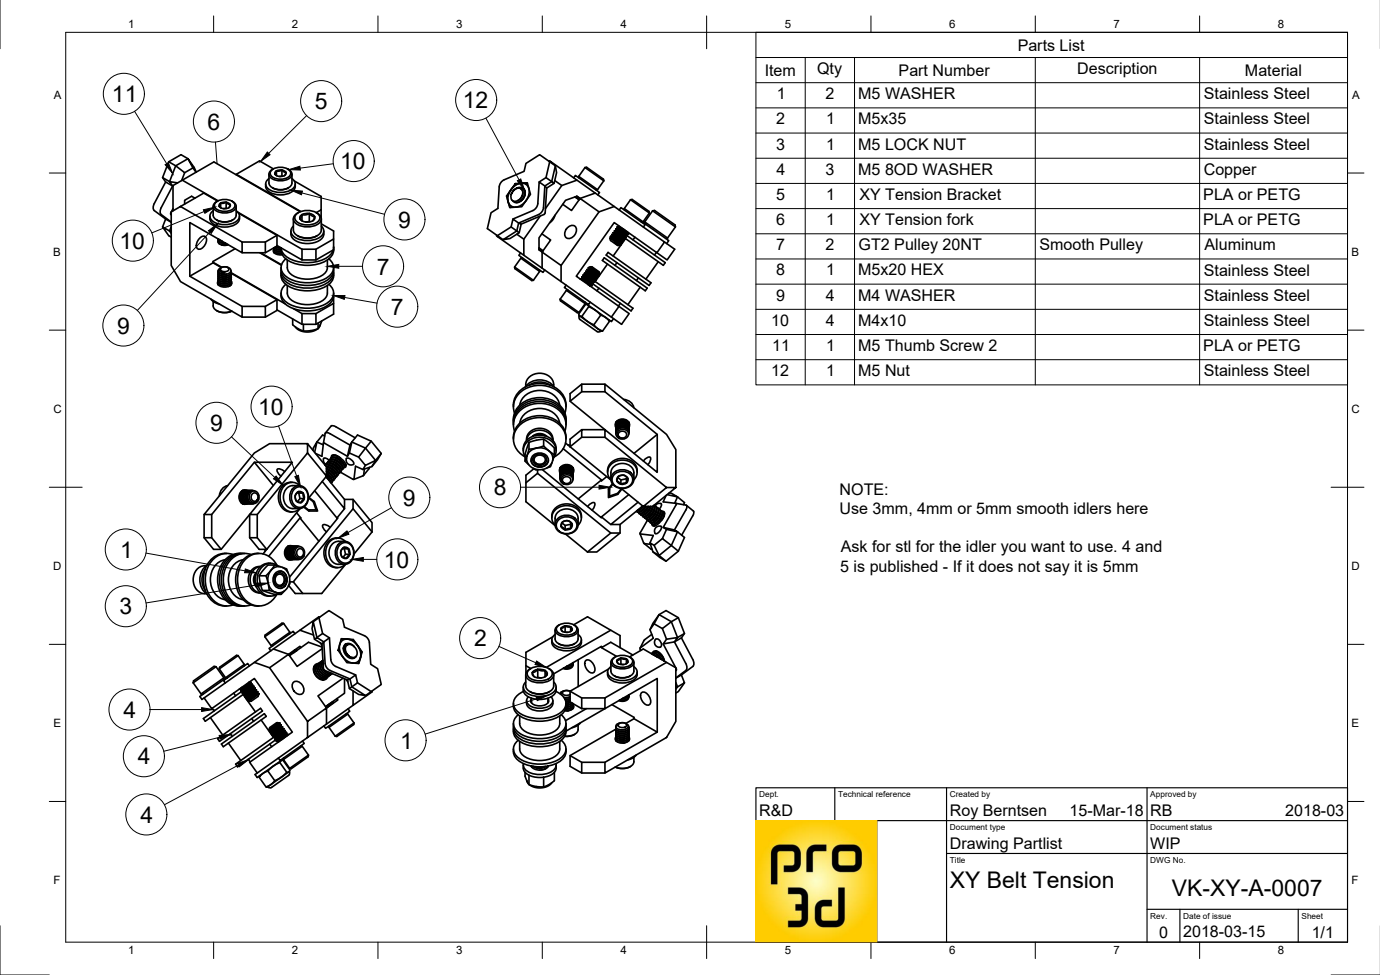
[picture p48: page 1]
8 BCDEF; ABCDEF; Parts List; Item; Qty; Part Number; Description; Material 1; M5 WASHER; Stainless Steel 2; Stainless Steel 3; M5 LOCK NUT; Stainless Steel 4; M5 8OD WASHER; Copper 5; XY Tension Bracket; PLA or PETG 6; XY Tension fork; PLA or PETG 7; GT2 Pulley 20NT; Smooth Pulley; Aluminum 8; M5x20 HEX; Stainless Steel 9; M4 WASHER; Stainless Steel; M5 Nut; Stainless Steel 6; NOTE:

10 | 4 | M4x10 | Stainless Steel
11 | 1 | M5 Thumb Screw 2 | PLA or PETG

Use 3mm, 4mm or 5mm smooth idlers here

Ask for stl for the idler you want to use. 4 and
5 is published - If it does not say it is 5mm

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

Document type Drawing Partlist | Document status WIP

Title | DWG No. VK-XY-A-0007 XY Belt Tension

Rev. | Date of issue 2018-03-15 | Sheet 0 1/1

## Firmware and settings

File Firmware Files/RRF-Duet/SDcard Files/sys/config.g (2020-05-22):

; Configuration file for Duet WiFi (firmware version 3)
; executed by the firmware on start-up
;
; generated by RepRapFirmware Configuration Tool v2.1.8 on Mon May 18 2020 20:36:22 GMT+0200 (Central European Summer Time)

; General preferences
G90                                            ; send absolute coordinates...
M83                                            ; ...but relative extruder moves
M550 P"V-King CXY"                             ; set printer name

M667 S1                                        ; select CoreXY mode

; Network
M552 S1                                        ; enable network
M586 P0 S1                                     ; enable HTTP
M586 P1 S0                                     ; disable FTP
M586 P2 S0                                     ; disable Telnet

; Panel Due
M575 P1 S1 B57600								enable panel due connector

; Drives
M569 P0 S1                                     ; physical drive 0 goes forwards
M569 P1 S1                                     ; physical drive 1 goes forwards
M569 P2 S1                                     ; physical drive 2 goes forwards
M569 P3 S1                                     ; physical drive 3 goes forwards
M584 X0 Y1 Z2 E3                               ; set drive mapping
M350 Z16 E16 I0                                ; configure microstepping without interpolation
M350 X16 Y16 I1                                ; configure microstepping with interpolation
M92 X80.00 Y80.00 Z3200.00 E406.00             ; set steps per mm
M566 X900.00 Y900.00 Z150.00 E600.00           ; set maximum instantaneous speed changes (mm/min)
M203 X18000.00 Y18000.00 Z600.00 E18000.00     ; set maximum speeds (mm/min)
M201 X3000.00 Y3000.00 Z120.00 E1000.00        ; set accelerations (mm/s^2)
M906 X1000 Y1000 Z600 E1000 I30                ; set motor currents (mA) and motor idle factor in per cent
M84 S30                                        ; Set idle timeout

; Axis Limits
M208 X0 Y0 Z0 S1                               ; set axis minima
M208 X340 Y390 Z330 S0                         ; set axis maxima

; Endstops
M574 X1 S1 P"xstop"                            ; configure active-high endstop for low end on X via pin xstop
M574 Y1 S1 P"ystop"                            ; configure active-high endstop for low end on Y via pin ystop
M574 Z1 S2                                     ; configure Z-probe endstop for low end on Z

; Z-Probe
M950 S0 C"exp.heater3"                         ; create servo pin 0 for BLTouch
M558 P9 C"zprobe.in+zprobe.mod" H5 F120 T18000 A30 S0.02 ; set Z probe type to bltouch and the dive height + speeds
G31 P500 X0 Y35 Z1.2                            ; set Z probe trigger value, offset and trigger height
M557 X26:340 Y30:370 S78:85                    ; define mesh grid

; Heaters
M308 S0 P"bedtemp" Y"thermistor" T100000 B4138 ; configure sensor 0 as thermistor on pin bedtemp
M950 H0 C"bedheat" T0                          ; create bed heater output on bedheat and map it to sensor 0
M143 H0 S120                                   ; set temperature limit for heater 0 to 120C
M307 H0 B0 S1.00                               ; disable bang-bang mode for the bed heater and set PWM limit
M140 H0                                        ; map heated bed to heater 0
M308 S1 P"e0temp" Y"pt1000" R4700              ; configure sensor 1 as PT1000 on pin e0temp
M950 H1 C"e0heat" T1                           ; create nozzle heater output on e0heat and map it to sensor 1
M143 H1 S300                                   ; set temperature limit for heater 1 to 300C
M307 H1 B0 S1.00                               ; disable bang-bang mode for heater  and set PWM limit

; Fans
M950 F0 C"fan0" Q500                           ; create fan 0 on pin fan0 and set its frequency
M106 P0 S0 H-1                                 ; set fan 0 value. Thermostatic control is turned off
M950 F1 C"fan1" Q500                           ; create fan 1 on pin fan1 and set its frequency
M106 P1 S1 H1 T100                              ; set fan 1 value. Thermostatic control is turned on
M950 F2 C"fan2" Q500                           ; create fan 2 on pin fan2 and set its frequency
M106 P2 S1 H1 T180                             ; set fan 2 value. Thermostatic control is turned on

; Tools
M563 P0 D0 H1 F0                               ; define tool 0
G10 P0 X0 Y0 Z0                                ; set tool 0 axis offsets
G10 P0 R0 S0                                   ; set initial tool 0 active and standby temperatures to 0C

; Custom settings are not defined

; Miscellaneous
M501                                           ; load saved parameters from non-volatile memory
T0                                             ; select first tool

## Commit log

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2018-03-04 Add files via upload
    Initial upload - Y Slider and assembly partlist drawing
    [M5 ThumbScrew.stl, Slider Fork.stl, Y-Slide Top.stl]
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2018-03-05 Add files via upload
    idler brackets for x axis
    [Idler X Bracket L.stl, Idler X Bracket R.stl]
2018-03-07 Add files via upload
    Initial uload of stl files only
    [M5 ThumbScrew.stl, Slider Fork.stl]
2018-03-08 Add files via upload
    more files for z - drawings must follow - happy printing
    [Belt Stop Washer.stl, GT2 Z Buddy.stl, Worm Gear Buddy.stl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]
2018-03-08 Add files via upload
    Last XY parts to print
    [XY Tension Bracket.stl, XY Tension Fork.stl]
2018-03-08 Add files via upload
    Tension for XY uploaded
    [XY Tension Bracket.stl, XY Tension Fork.stl]
2018-03-08 Delete Z-Slide Top.stl
    to tight on the corner - update tomorrow
    [Z-Slide Top.stl]
2018-03-08 Add files via upload
    fixed tight corner
    [Z-Slide Top.stl]
2018-03-09 Add files via upload
    changed the z-slide top for some better clearance to the aluminum extrusion
    [Z-Slide Top.stl]
2018-03-09 Add files via upload
    design changes for better stability as there was some movment
    [Z Belt Buddy Base.stl, Z Belt Buddy Tension.stl]
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2018-03-09 Delete Z Bed Belt Buddy Base.stl
    new file for this part uploaded
    [Z Bed Belt Buddy Base.stl]
2018-03-09 Delete Z Bed Belt Tension Buddy.stl
    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
    [Z Bed Belt Tension Buddy.stl]
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2018-03-10 Design change
    Minor detail design changes to X carry
    [Belt Lock A.stl, Belt Lock B.stl, M5 ThumbScrew.stl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]
2018-03-10 Design change
    added a V to the Y top slider part for better alignment
    [Y-Slide Top.stl]
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2018-03-10 adjustment of support
    added longer support wall for the clamp space in X top for better print result
    [X-Slide Top.stl]
2018-03-10 added support wall
    In the clamp attach space I needed one more thin wall
    [X-Slide Top.stl]
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2018-03-15 XY Revised all good!
    Revised XY Parts and drawings all ready and good to go
    Still working on Z mods
    [Belt Lock A.stl, Belt Lock B.stl, Idler X Bracket L.stl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]
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2018-03-16 Removing and adding some Z parts
    will uploade complete kit next week
    [Belt Anchor M.stl, Belt Anchor R.stl, Belt Stop Washer.stl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]
2018-03-18 New pulley brackets for Z axis
    with belt anchor
    [Z-Pulley Top Belt Lock.stl, Z-Pulley Top M.stl, Z-Pulley Top R.stl]
2018-03-19 License
    All files are released according to the following license unless specified differently in the file or directory:
    [Filament Holder Nut.stl, Filament Holder Rod.stl]
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2018-03-21 added marlin config h + adv
    changed name on some parts
    [Configuration_adv.h, PSU+SSR Cabinet.stl, PSU+SSR Lid 80Fan.stl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]
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2018-03-22 encreased shell
    on psu cabinet from 2 to 3mm
    [PSU+SSR Cabinet.stl, PSU+SSR Lid 80Fan.stl, VK-PSU-Case.stl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]
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2018-04-06 added vking pro 4 source files
    slider Y top and slider fork
    [Slider Fork v1.step, Slider Fork.f3d, VK-PSU-Lid-60Fan.stl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]
2018-04-06 updated bed idler support
    now 3mm before 4mm
    [Bed Idler Support.stl]
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2018-04-10 Minor changes to Z slide
    added screws to bom and changed the slot extrusion
    [12864 LCD Back Cover V2.stl, 12864 LCD Front Lid V2.stl, MKSBerry Lid.stl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]
2018-04-10 updatet bom fastners only
    M5x10+washers 8 of each
    [V-King PRO 3D 400 BOM.xlsx]
2018-04-12 added titan - nema bracket to xy part files and source files
    [Nema-Titan Bracket.step, Nema-Titan Bracket.stl]
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2018-04-13 Added source files - X top Slide stp
    [Belt Lock A.stl, Belt Lock B.stl, X Belt lock Bottom.stl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]
2018-04-14 updated Z belt anchor
    Can still use the old. This is just to improve some thine areas
    [Z Belt Anchor M.step, Z Belt Anchor M.stl, Z Belt Anchor R.step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]
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2018-04-15 added source files - updated bed idler bracket
    4 to 5 mm on bed idler bracket
    [Bed Idler Buddy.step, Bed Idler Buddy.stl, Bed Idler Support.step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]
2018-04-17 added source files - changed some part names
    no important changes to design
    [12864 LCD Back Cover V2.stl, EndStop Bracket X Far Side.step, EndStop Bracket X Far Side.stl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]
2018-04-18 updated config.h and added spacer
    spacer for BLT changed some names
    [BL Touch Spacer -1.stl, Body2.stl, Configuration.h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]
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2018-04-30 Design Improvment to the X Idlers
    new bracket for better support
    [4020 Blower Layer Fan cover-shroud.stl, Body2.stl, End Stop X Bracket.stl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]
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2018-05-03 Upgrades on X Carrier and X idler brackets
    New carrier and idler brackets for belts on the side to awoid binding and get more X movement
    [BL Touch Spacer -1.stl, BL Touch Spacer.stl, Belt Lock X Lower.stl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]
2018-05-04 Corrected Z-Slide Chamfer
    [Z-Slide Top.stl]
2018-05-04 Corrected Z-Slide Chamfer to source file
    [Z-Slide Top.step]
2018-05-04 Updated worgear with 5mm holes for anchors
    Updated worgear with 5mm holes for anchors instead of 4mm
    [Worm Gear Buddy.step, Worm Gear Buddy.stl, Worm Gear Rod Buddy.step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]
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2018-05-05 updated bed supports
    from 4 to 5mm holes
    [Bed Thumb Screw.step, Bed Thumb Screw.stl, Bed Top Support.step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]
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2018-05-09 redesigned L bracket for printing purposes
    [3010 V6 HeatSink FanShroud.stl, Bed Profile L Bracket.step, Bed Profile L Bracket.stl]
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2018-05-14 Updated silicone heater link
    link was wrong dimension - ask for more power
    [V-King PRO 3D 400 BOM.xlsx]
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2018-05-16 small cosmetic change to lower belt lock
    diameter change due to slicing better
    [V-Slide Belt Lock X Lower.stl]
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2018-06-18 added short version single loop belt buddy
    [Z Single Loop Belt Buddy - Short.stl]
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2018-07-06 error check
    [V-King PRO 400 Part Order List.xlsx]
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2018-07-19 Updated stl folder with readme file for slicer recommendation
    pictures of orientation and infill%
    [XY Tension Bracket_2x.stl, XY Tension Fork_2x.stl]
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2018-08-29 updated X endstop flag - corrected height
    [X EndStop Flag_1x.stl]
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2018-08-31 updated tool holder with better hole tolerance
    [ToolHolder.stl]
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2018-09-18 changing name on upgrade folder to optional stl
    also adding x carrier clean
    [5015 Layer Fan Bracket.stl, 5015 Layer Fan Shroud.stl, 5020 Layer Fan Bracket.stl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]
2018-09-20 updated firware with latest bugfix
    [Configuration.h, Configuration_adv.h]
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2018-09-23 Encreased the motor bracket for better placement of corner supports
    Just minor changes
    [XY Motor Corner Bracket_2x.stl]
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2018-09-26 Uodated missing links on pdf
    [V-King PRO 400 Part Order List.xlsx]
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2018-09-27 fixed a link
    [V-King PRO 400 Part Order List.xlsx]
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2018-10-28 Change some tolerances on fork and belt locks
    [3020 Cylinder.stl, 5015 LF Shroud.stl, 5015 Layer Fan Bracket Front.stl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]
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2018-12-29 Update 5015 Layer Fan Shroud.stl
    1mm rarrower due to contact with carrier
    [5015 Layer Fan Shroud.stl]
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2019-03-17 changed tolerances on lock
    [Z Belt Anchor Low M_1x.stl, Z Belt Lock Low M_1x.stl]
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2019-05-17 removed assy not working
    [Build Plate Support Assy.f3d]
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
